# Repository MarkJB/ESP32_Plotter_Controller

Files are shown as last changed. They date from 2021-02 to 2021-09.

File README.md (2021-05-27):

# ESP32 Plotter Controller PCB
 
Released under an MIT licence, no warranty implied or given, use at own risk etc etc.

This is a two axis stepper controller based on the ESP32 and TMC2130 stepper drivers. It is intended to be used with drawing machines and plotters.

See https://github.com/MarkJB/TMC429_Daughterboard_for_ESP32_Plotter_Controller for the TMC429 (Hardware stepper driver contoller) daughter board for this board (plugs into the two stepper motor driver sockets and provides an extra axis and hardware acceleration control.

Firmware https://github.com/MarkJB/Grbl_Esp32 (This is a Fork of Grbl_Esp32, if its out of date, you probably only need the config file from this fork). Tested with standard and corexy kinematics and a solenoid/relay for the spindle.

First board revision A (aka 'Diamiond Chimp')

[Schematic]( https://github.com/MarkJB/ESP32_Plotter_Controller/blob/main/ESP32_Plotter_Controller_Schematic_RevA.pdf )

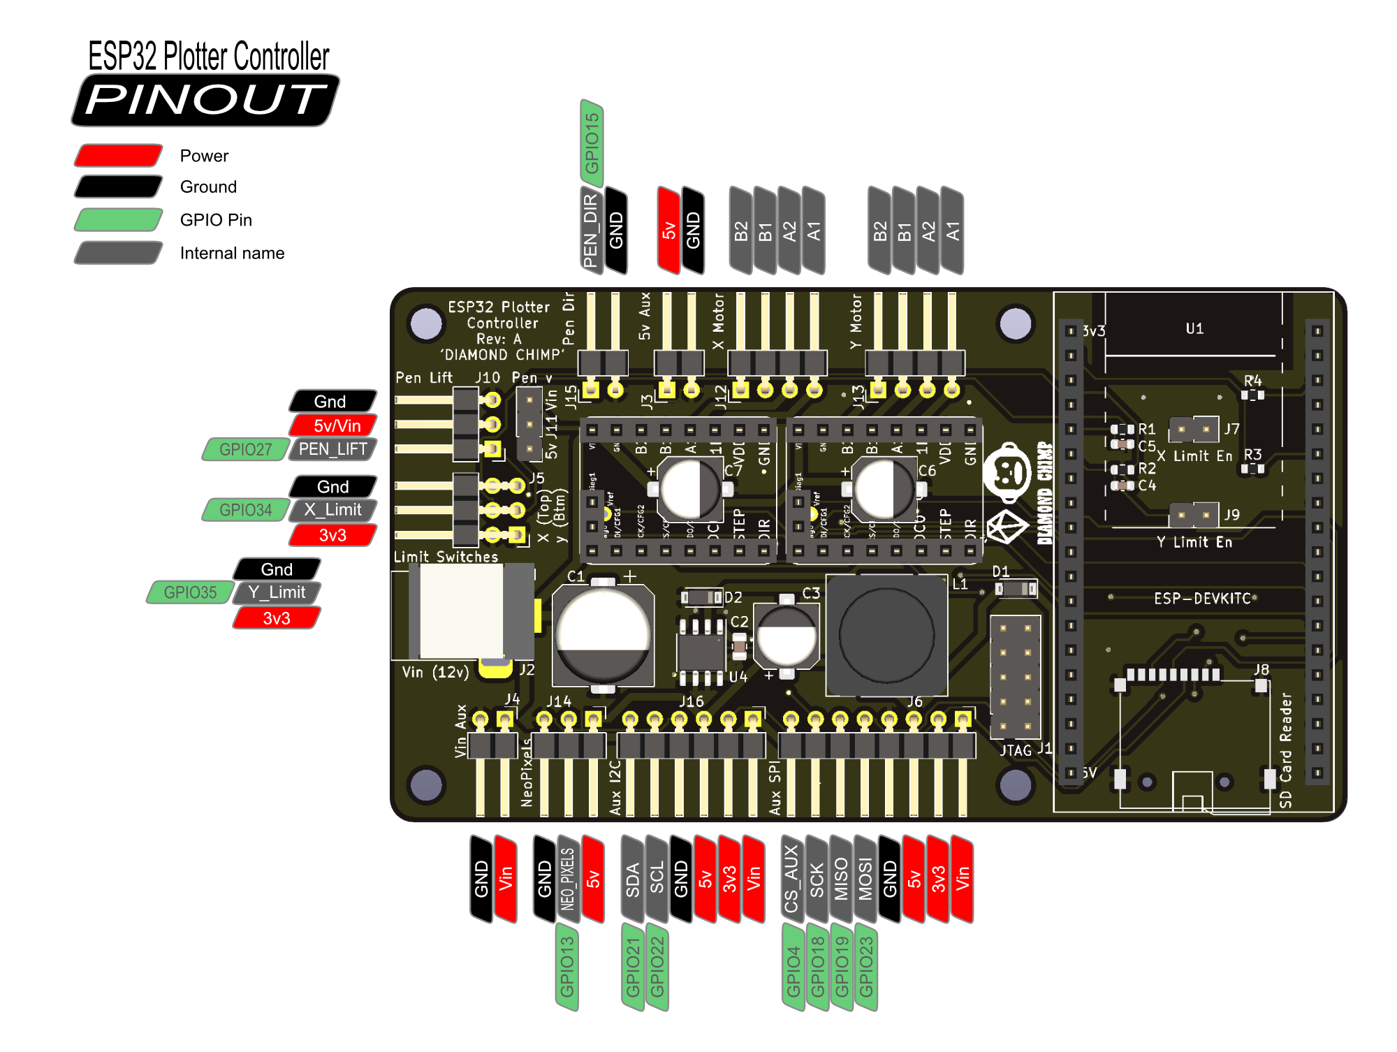
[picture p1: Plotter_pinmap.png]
Pinmap


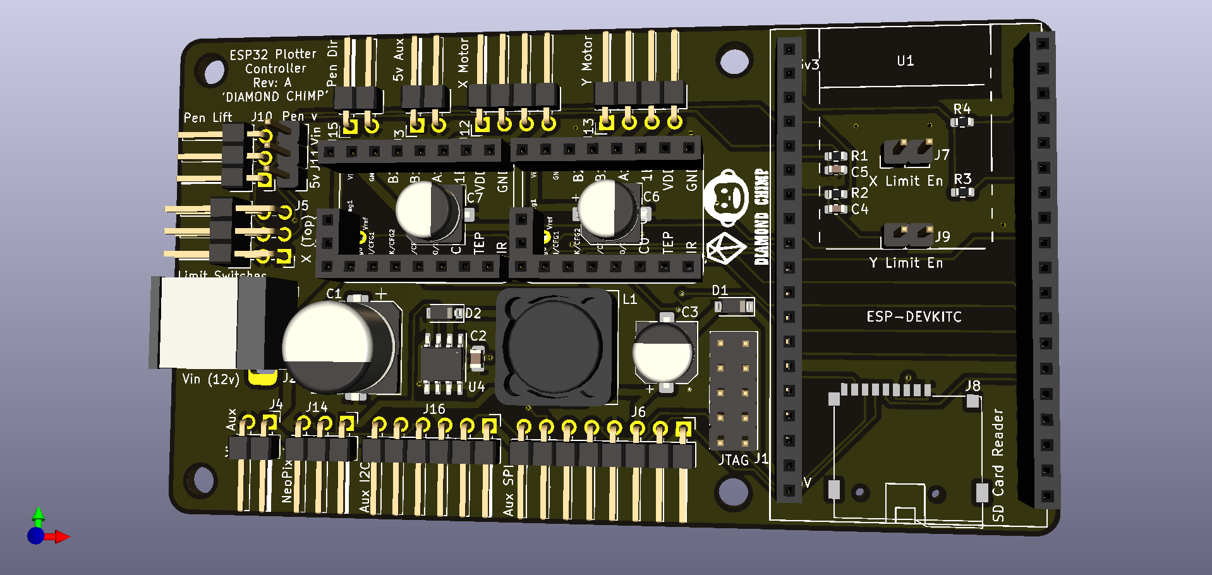
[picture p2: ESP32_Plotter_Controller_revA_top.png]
Render of top of board


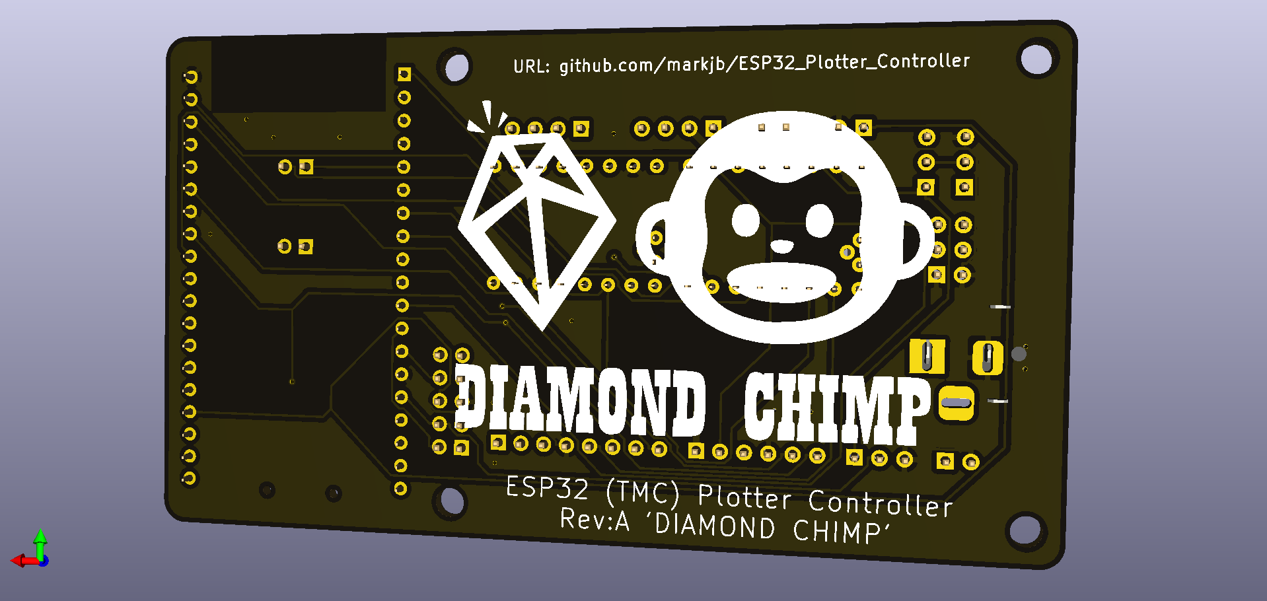
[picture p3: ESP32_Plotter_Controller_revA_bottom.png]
Render of bottom of board


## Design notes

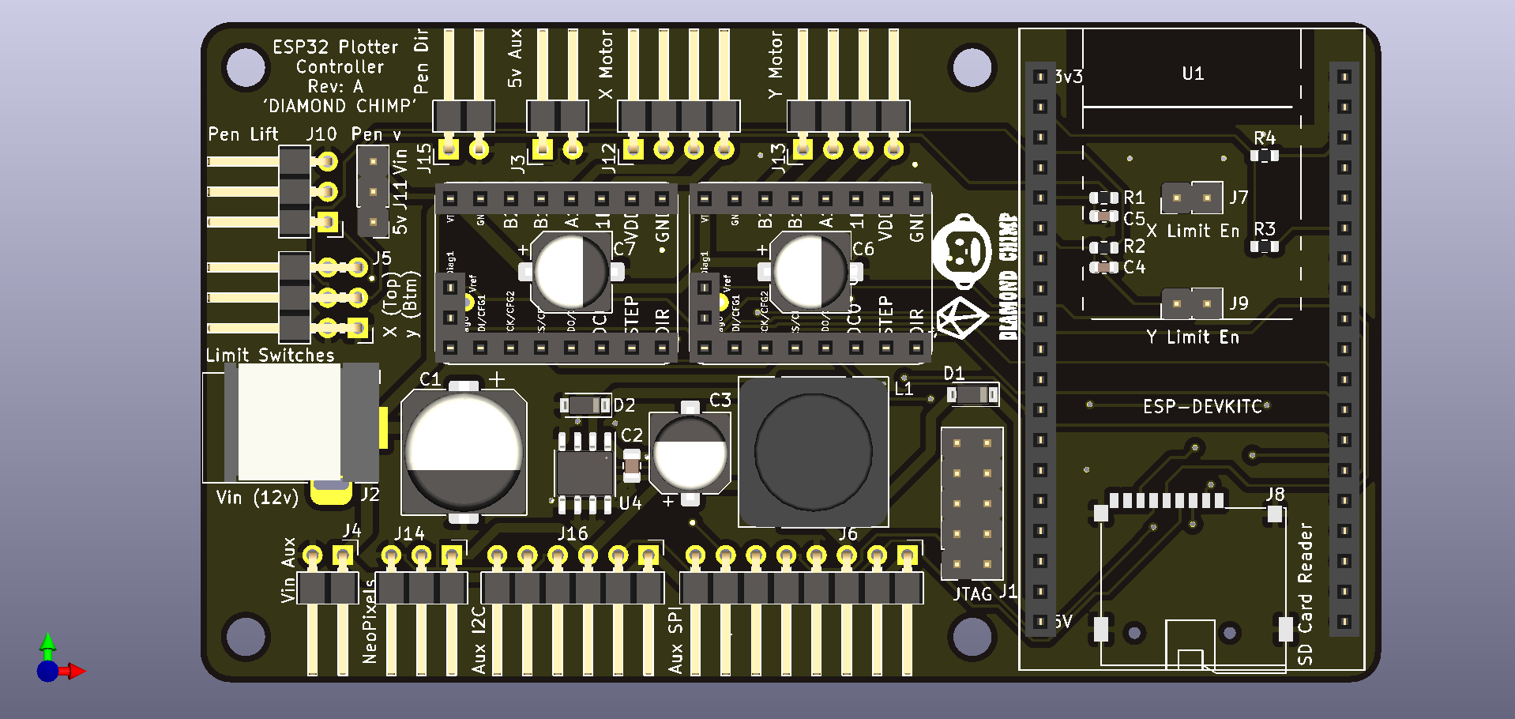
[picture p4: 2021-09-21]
ESP32_Plotter_Controller_revA_top_projection.png

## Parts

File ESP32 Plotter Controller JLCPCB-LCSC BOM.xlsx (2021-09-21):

 | ESP32 Plotter Controller parts cross check
 | PCB Part # | Value | Package | Board Note | Check Footprint | JLC part | JLC price | Package | LCSC part | LCSC price | Package | Qty (per board)
 | J1 | n/a | 5x2 vertical female 2.54mm | JTAG | TBD | No |  |  | C492399 | 0.1488 |  | 1
 | J2 | DC-005-20A | DC Barel jack | Power in | TBD | Yes | 0.179 | 14.2*9.0mm | C130239 | 0.1023 |  | 1
 | J3 | n/a | 2x1 right angle male 2.54mm | 5v aux | n/a | Yes | 0.0049 |  | C492410 | 0.012 |  | 1
 | J4 | n/a | 2x1 right angle male 2.54mm | 12v aux | n/a | Yes | 0.0049 |  | C492410 | 0.012 |  | 1
 | J5 | n/a | 3x2 right angle male 2.54mm | Limit Switches | n/a | No |  |  | C358705 | 0.0342 |  | 1
 | J6 | n/a | 8x1 right angle male 2.54mm | SPI port | n/a | No |  |  | C376126 | 0.0481 |  | 1
 | J7 | n/a | 2x1 vertical male 2.54mm | X Limit en | n/a | Yes | 0.0049 |  | C492401 | 0.0049 |  | 1
 | J8 | n/a | Micro SD card socket | SD card female | TBD | No |  |  | C91145 | 0.178 |  | 1
 | J9 | n/a | 2x1 vertical male 2.54mm | Y Limit en | n/a | Yes | 0.0049 |  | C492401 | 0.0049 |  | 1
 | J10 | n/a | 3x1 right angle male 2.54mm | Pen Lift | n/a | No |  |  | C492411 | 0.0199 |  | 1
 | J11 | n/a | 3x1 vertical male 2.54mm | Pen Lift voltage select | n/a | No |  |  | C306223 | 0.345 |  | 1
 | J12 | n/a | 4x1 right angle male 2.54mm | X Motor | n/a | No |  |  | C91552 | 0.0189 |  | 1
 | J13 | n/a | 4x1 right angle male 2.54mm | Y Motor | n/a | No |  |  | C91552 | 0.0189 |  | 1
 | J14 | n/a | 3x1 right angle male 2.54mm | Neo Pixels | n/a | No |  |  | C492411 | 0.0199 |  | 1
 | J15 | n/a | 2x1 right angle male 2.54mm | Pen Direction | n/a | Yes | 0.0049 |  | C492410 | 0.012 |  | 1
 | U1 | n/a | 19x1 vertical female 2.54mm | ESP32 DevkitC | TBD | No |  |  | C319202 | 0.1119 |  | 1
 | U1 | n/a | 19x1 vertical female 2.54mm | ESP32 DevkitC | TBD | No |  |  | C319202 | 0.1119 |  | 1
 | U2 | n/a | 8x1 vertical female 2.54mm | TMC2130 Stepper X | TBC | No |  |  | C429957 | 0.1119 |  | 1
 | U2 | n/a | 8x1 vertical female 2.54mm | TMC2130 Stepper X | TBC | No |  |  | C429957 | 0.0622 |  | 1
 | U2 | n/a | 2x1 vertical female 2.54mm | TMC2130 Stepper X | TBC | No |  |  | C541849 | 0.0723 |  | 1
 | U3 | n/a | 8x1 vertical female 2.54mm | TMC2130 Stepper Y | TBC | No |  |  | C429957 | 0.0622 |  | 1
 | U3 | n/a | 8x1 vertical female 2.54mm | TMC2130 Stepper Y | TBC | No |  |  | C429957 | 0.0622 |  | 1
 | U3 | n/a | 2x1 vertical female 2.54mm | TMC2130 Stepper Y | TBC | No |  |  | C541849 | 0.0723 |  | 1
 | U4 | XL1509 | SO-8_3.9x4.9mm_P1.27mm | DCDC converter | TBC |  |  |  | C61063 | 0.2268 |  | 1
 | D1 | B5819W | SOD-123 | Reverse current protection | TBC | Yes | 0.0344 | SOD-123 | C8598 | 0.0404 |  | 1
 | D2 | B5819W | SOD-123 | DCDC converter | TBC | Yes | 0.0344 | SOD-123 | C8598 | 0.0404 |  | 1
 | C1 | 470uF 25v SMT Elec | CP_ELEC_10x10 | DCDC converter | TBC | No |  |  | C280412 | 0.1255 |  | 1
 | C2 | 1uF 25v | 0805 | DCDC converter | TBC | Yes | 0.0526 |  | C28323 | 0.0163 |  | 1
 | C3 | 180uF 25v SMT Elec | CP_ELEC_6.3x7.7 | DCDC converter | TBC | Yes | 0.166 |  | C413657 | 0.3033 |  | 1
 | C4 | 100nF | 0603 | Y Limit debounce | TBC | No |  |  | C42998 | 0.0032 |  | 1
 | C5 | 100nF | 0603 | X Limit debounce | TBC | No |  |  | C42998 | 0.0032 |  | 1
 | C6 | 47uF | CP_ELEC_6.3x5.7 | Y Stepper resivoir | TBC |  |  |  | C176688 | 0.1016 |  | 1
 | C7 | 47uF | CP_ELEC_6.3x5.7 | X Stepper resivoir | TBC |  |  |  | C176688 | 0.1016 |  | 1
 | R1 | 100R | 0603 | X Limit debounce | TBC | Yes | 0.0013 |  | C25201 | 0.0013 |  | 1
 | R2 | 100R | 0603 | Y Limit debounce | TBC | Yes | 0.0013 |  | C25201 | 0.0013 |  | 1
 | R3 | 10K | 0603 | I2C Pull up (SDA) | TBC | No |  |  | C98220 | 0.0015 |  | 1
 | R4 | 10K | 0603 | I2C Pull up (SCL) | TBC | No |  |  | C98220 | 0.0015 |  | 1
 | L1 | 68uH 1.5A | SMD, 12.3x12.3x6mm | DCDC converter | TBC |  |  |  | C439406 | 0.232 |  | 1
 | PCB | Guestimate |  |  |  |  |  |  |  | 5
 | Assembly | Guestimate |  |  |  |  |  |  |  | 5
 |  |  |  |  |  |  |  |  |  | 12.8466
 | Component Order BOM (lcsc.com)
Ordered? | LCSC Part No: | Qty | PCB Part No: | Package | Value | Cost | Line Cost
n/a | C492399 | 1 | J1 | 5x2 vertical female 2.54mm |  | 0.1488 | 0.1488
Y | C130239 | 1 | J2 | DC Barrel jack |  | 0.1023 | 0.1023
no | C492410 | 2 | J3, J4, J15 | 2x1 right angle male 2.54mm |  | 0.012 | 0.024
Y | C358705 | 1 | J5 | 3x2 right angle male 2.54mm |  | 0.0342 | 0.0342
Y | C376126 | 1 | J6 | 8x1 right angle male 2.54mm |  | 0.0342 | 0.0342
Y | C492401 | 2 | J7, J9 | 2x1 vertical male 2.54mm |  | 0.0049 | 0.0098
Y | C492411 | 2 | J10, J14 | 3x1 right angle male 2.54mm |  | 0.0199 | 0.0398
Y | C306223 | 1 | J11 | 3x1 vertical male 2.54mm |  | 0.345 | 0.345
no | C91552 | 2 | J12, J13 | 4x1 right angle male 2.54mm |  | 0.0189 | 0.0378
Y | C91145 | 1 | J8 | Micro SD card socket |  | 0.178 | 0.178
Y | C319202 | 2 | U1 | 19x1 vertical female 2.54mm |  | 0.1119 | 0.2238
Y | C429957 | 4 | U2, U3 A | 8x1 vertical female 2.54mm |  | 0.1119 | 0.4476
Y | C541849 | 2 | U2, U3 B | 2x1 vertical female 2.54mm |  | 0.0723 | 0.1446
no | C61063 | 1 | U4 | SO-8_3.9x4.9mm_P1.27mm | XL1509 | 0.2268 | 0.2268
Y | C8598 | 2 | D1, D2 | SOD-123 | B5819W | 0.0404 | 0.0808
Y | C280412 | 1 | C1 | CP_ELEC_10x10 | 470uF 25v SMT Elec | 0.1255 | 0.1255
Y | C28323 | 1 | C2 | 0805 | 1uF 25v ceramic | 0.0163 | 0.0163
Y | C413657 | 1 | C3 | CP_ELEC_6.3x7.7 | 180uF 25v SMT Elec | 0.3033 | 0.3033
Y | C42998 | 2 | C4, C5 | 0603 | 100nF ceramic | 0.0032 | 0.0064
no | C176688 | 2 | C6, C7 | CP_ELEC_6.3x5.7 | 47uF 25v SMT Elec | 0.1016 | 0.2032
Y | C25201 | 2 | R1, R2 | 0603 | 100R | 0.0013 | 0.0026
Y | C98220 | 2 | R3, R4 | 0603 | 10k | 0.0015 | 0.003
Y | C439406 | 1 | L1 | L_12.3x12.3x6 SMT | 68uH 1.5A | 0.232 | 0.232
 |  |  |  |  |  |  | Total
 |  |  |  |  |  |  | 2.9698
 | Move capacitor nearer the dcdc chip, keep inductor feedback as short as possible, don't route under the inductor, connect en pin to via and leave floating

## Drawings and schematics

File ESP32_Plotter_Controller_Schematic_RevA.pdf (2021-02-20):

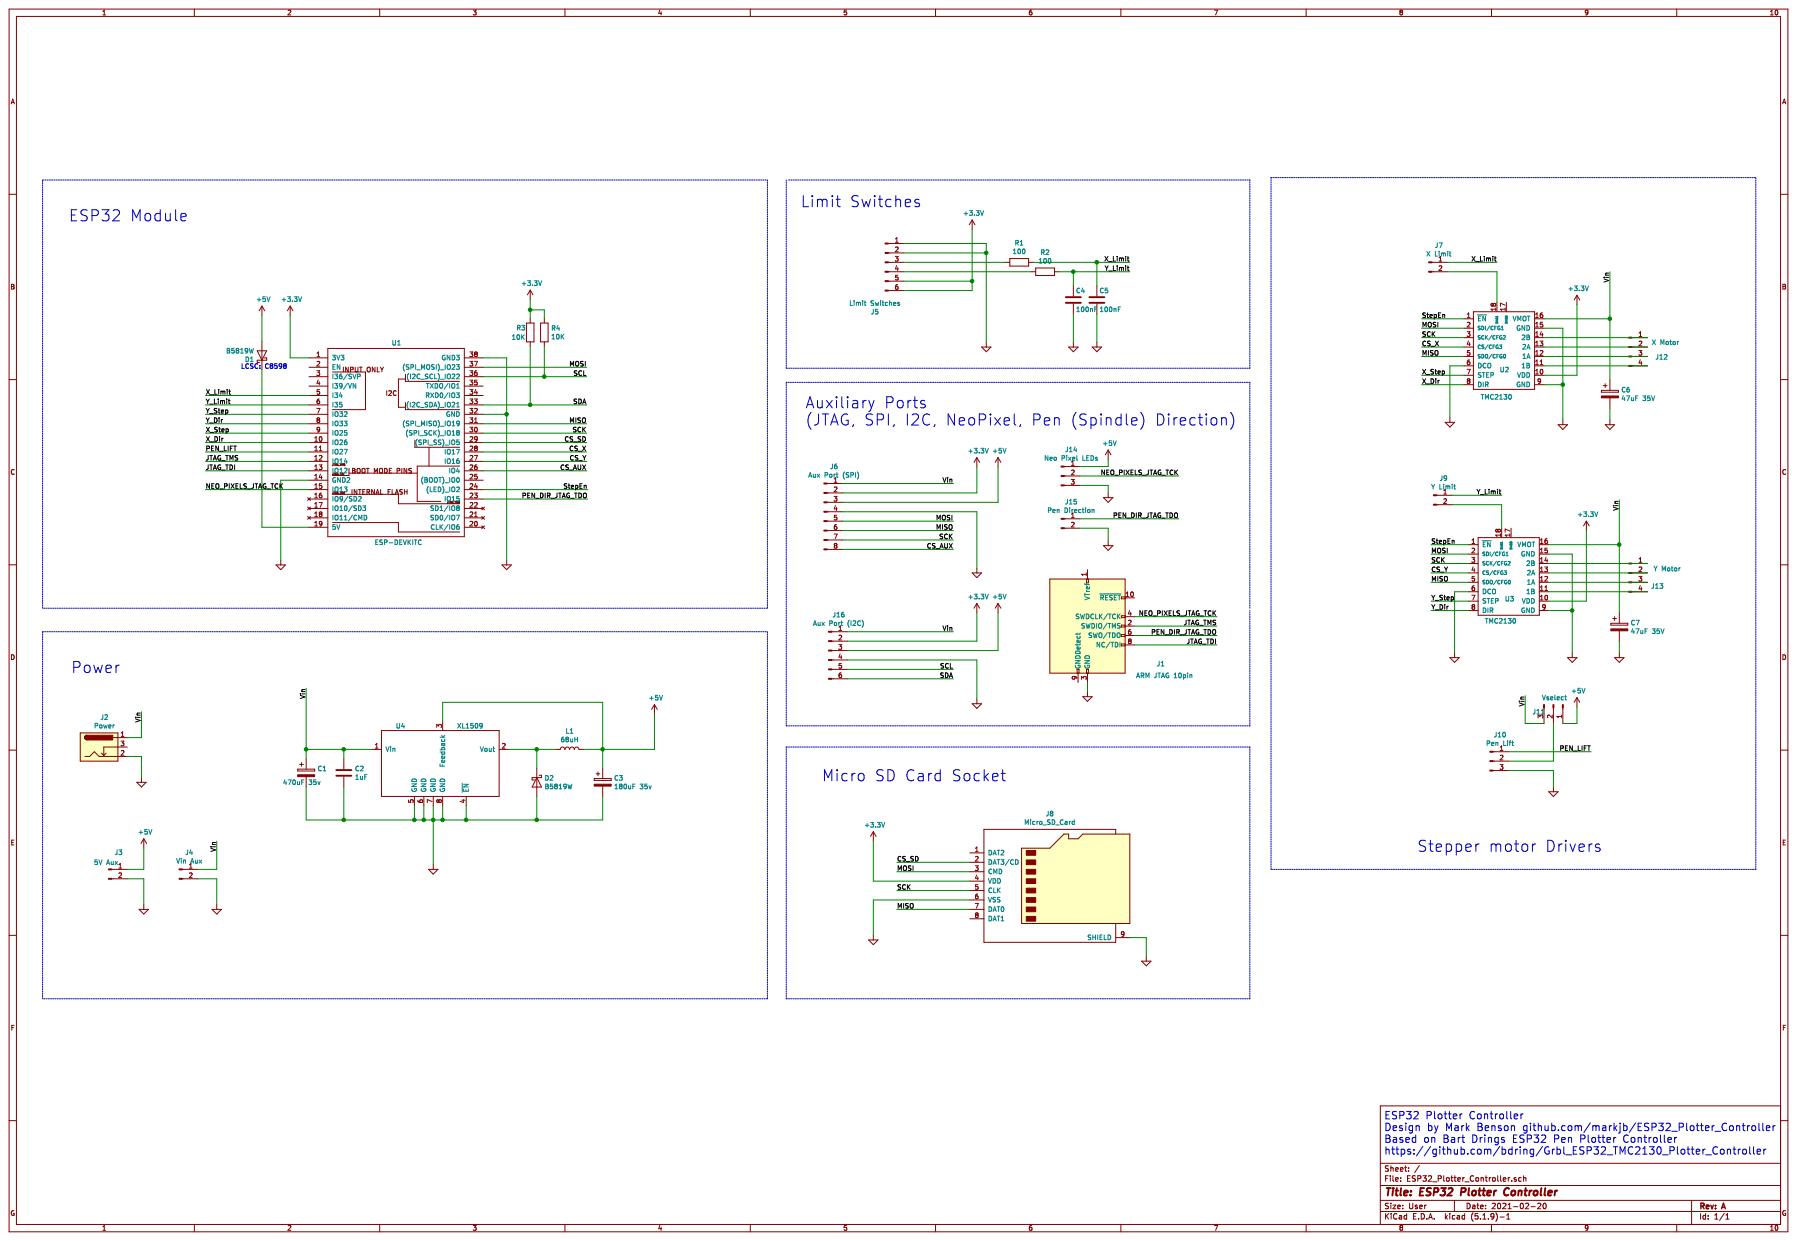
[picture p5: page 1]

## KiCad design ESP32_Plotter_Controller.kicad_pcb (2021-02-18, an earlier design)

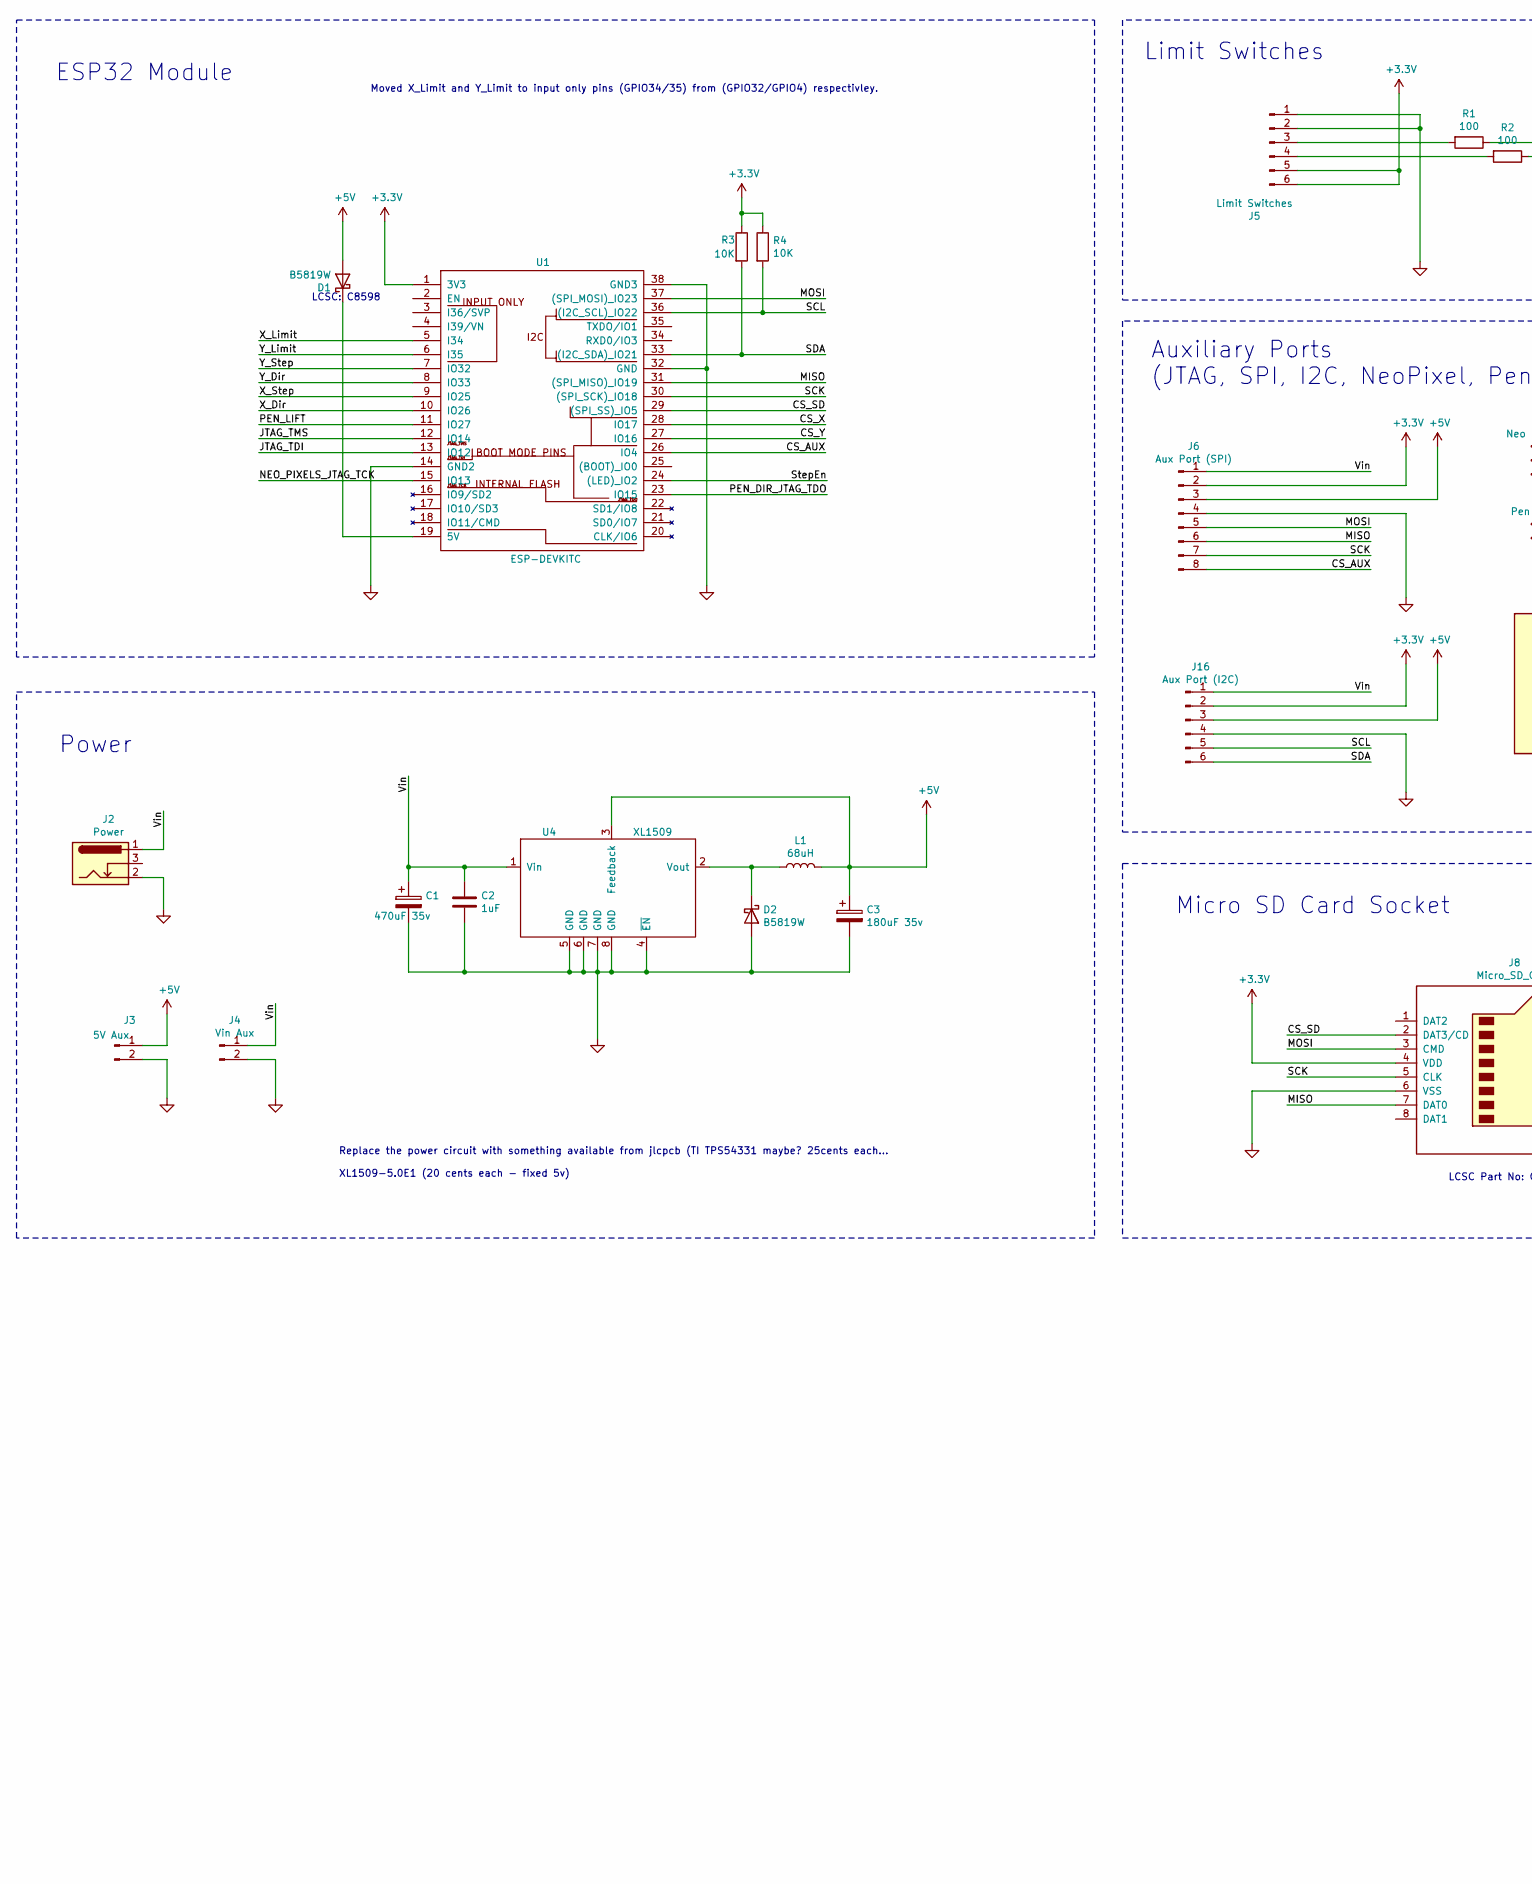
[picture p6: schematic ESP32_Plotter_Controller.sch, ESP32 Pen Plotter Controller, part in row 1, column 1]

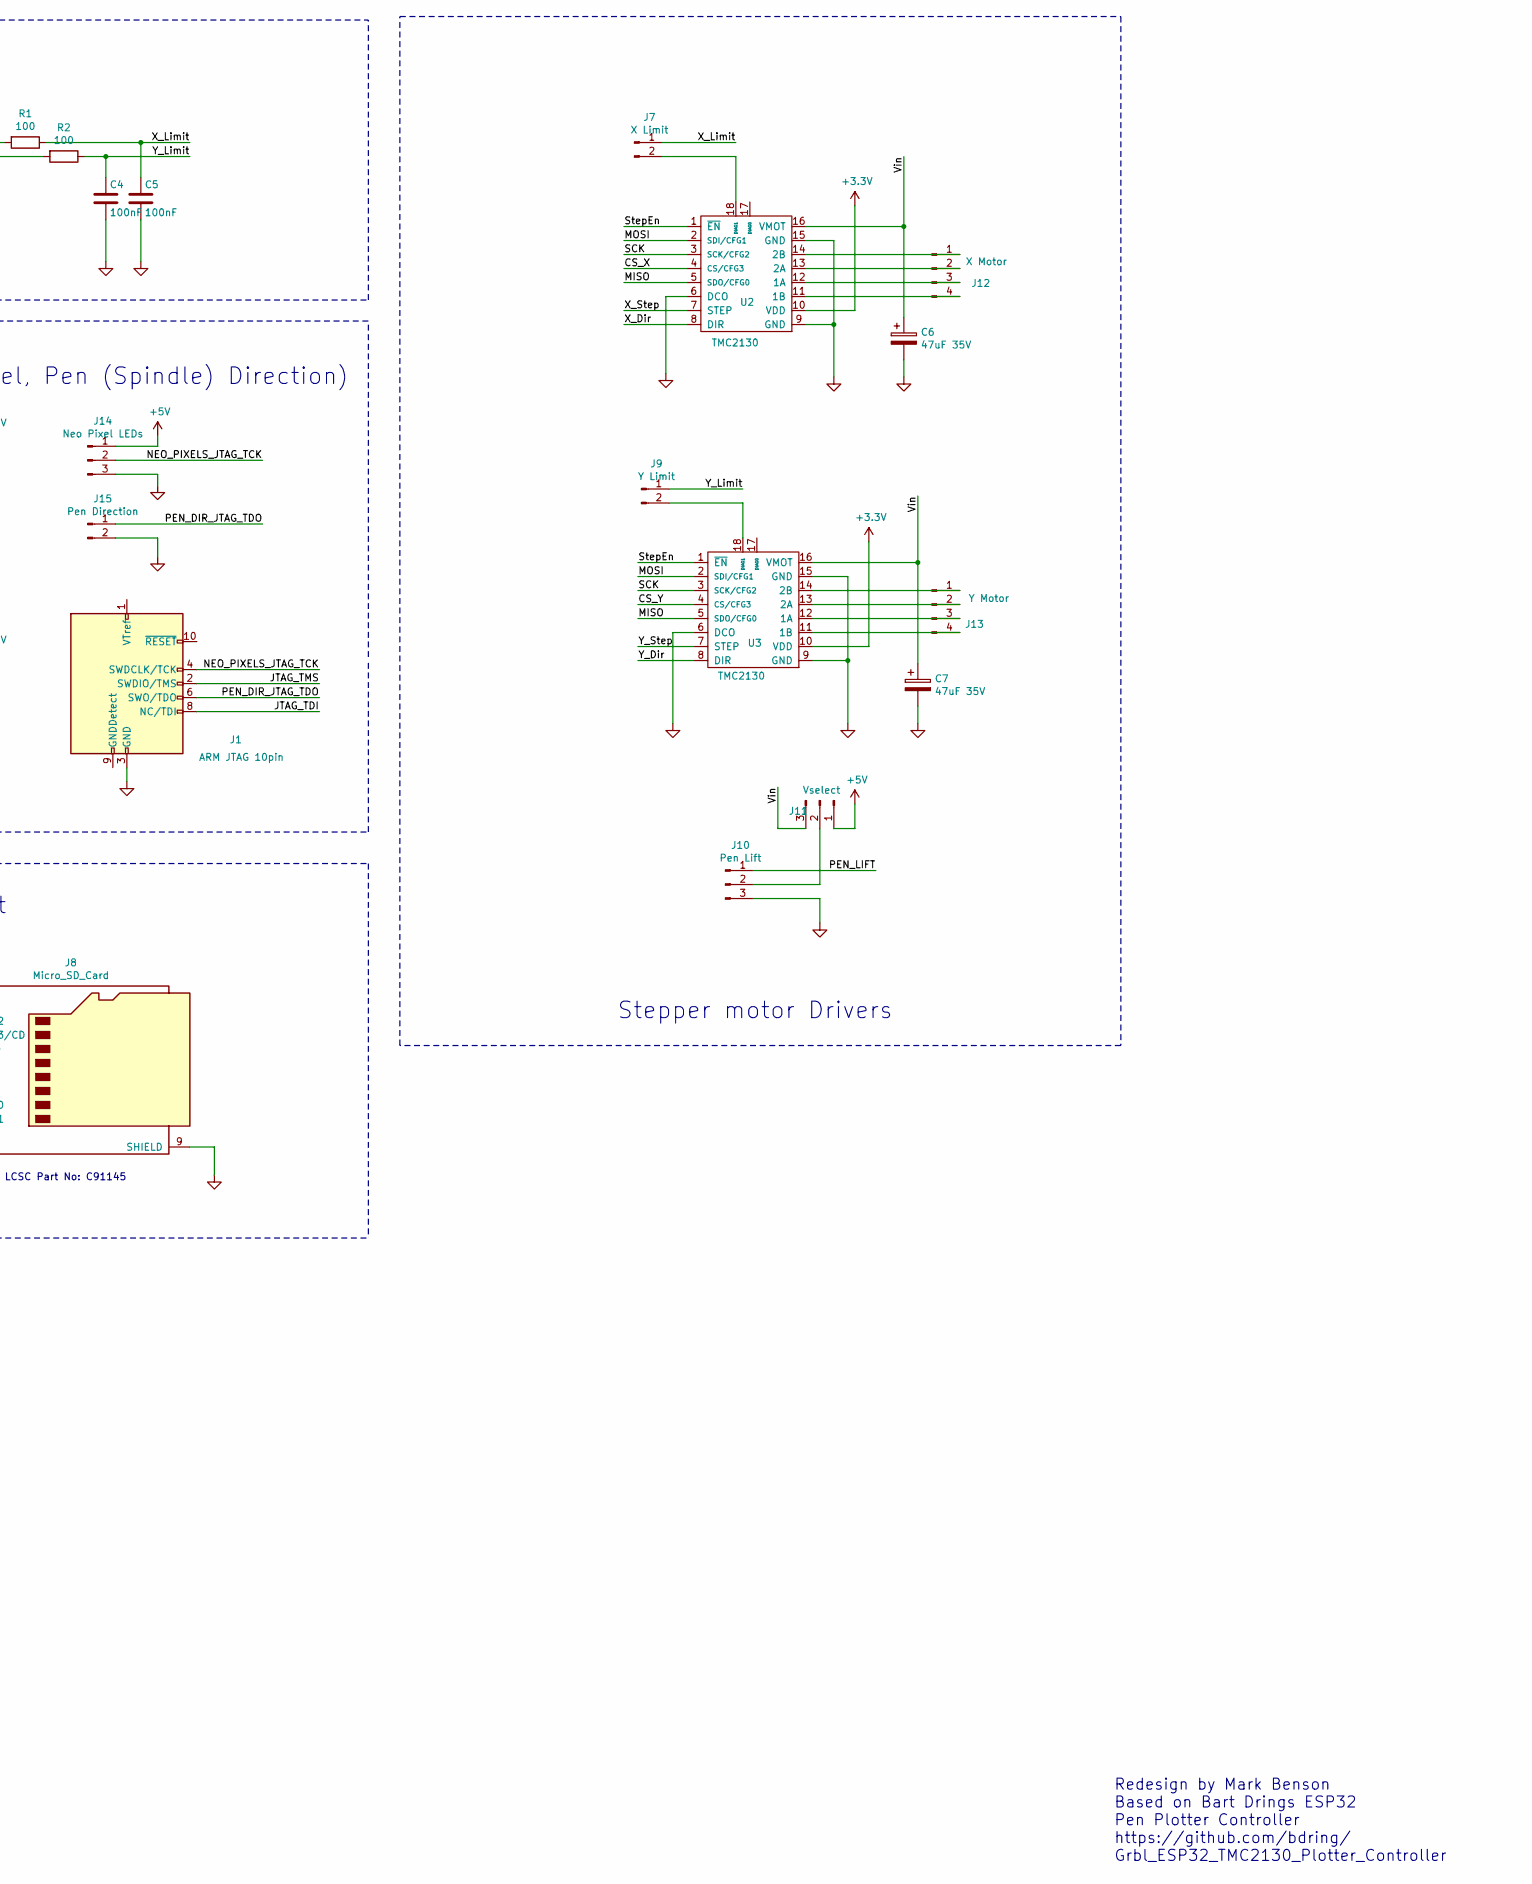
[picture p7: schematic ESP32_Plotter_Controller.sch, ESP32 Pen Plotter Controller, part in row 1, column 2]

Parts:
C1: 470uF 35v; CP_Elec_10x10
C2: 1uF; C_0805_2012Metric
C3: 180uF 35v; CP_Elec_6.3x7.7
C4, C5: 100nF; C_0603_1608Metric
C6, C7: 47uF 35V; CP_Elec_6.3x5.7
D1, D2: B5819W; D_SOD-123
J1: ARM JTAG 10pin; PinSocket_2x05_P2.54mm_Vertical
J2: Power; BarrelJack_Horizontal
J3: 5V Aux; PinHeader_1x02_P2.54mm_Horizontal
J4: Vin Aux; PinHeader_1x02_P2.54mm_Horizontal
J5: Limit Switches; PinHeader_2x03_P2.54mm_Horizontal
J6: Aux Port (SPI); PinHeader_1x08_P2.54mm_Horizontal
J7: X Limit; PinHeader_1x02_P2.54mm_Vertical
J8: Micro_SD_Card; HK-TF01A
J9: Y Limit; PinHeader_1x02_P2.54mm_Vertical
J10: Pen Lift; PinHeader_1x03_P2.54mm_Horizontal
J11: Vselect; PinHeader_1x03_P2.54mm_Vertical
J12: X Motor; PinHeader_1x04_P2.54mm_Horizontal
J13: Y Motor; PinHeader_1x04_P2.54mm_Horizontal
J14: Neo Pixel LEDs; PinHeader_1x03_P2.54mm_Horizontal
J15: Pen Direction; PinHeader_1x02_P2.54mm_Horizontal
J16: Aux Port (I2C); PinHeader_1x06_P2.54mm_Horizontal
L1: 68uH; L_12x12mm_H6mm
R1, R2: 100; R_0603_1608Metric
R3, R4: 10K; R_0603_1608Metric
U1: ESP-DEVKITC; DEVKITC
U2, U3: TMC2130; StepstickTMCv2
U4: XL1509; SO-8_3.9x4.9mm_P1.27mm

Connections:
+3V3: J5.5, J5.6, J6.2, J8.4 (VDD), J16.2, R3.1, R4.1, U1.1 (3V3), U2.10 (VDD), U3.10 (VDD)
+5V: C3.1, D1.2 (A), J3.1, J6.3, J11.1, J14.1, J16.3, L1.2, U4.3 (Feedback)
/CS_AUX: J6.8, U1.26 (IO4)
/CS_SD: J8.2 (DAT3/CD), U1.29 ((SPI_SS)_IO5)
/CS_X: U1.28 (IO17), U2.4 (CS/CFG3)
/CS_Y: U1.27 (IO16), U3.4 (CS/CFG3)
/JTAG_TDI: J1.8 (NC/TDI), U1.13 (IO12)
/JTAG_TMS: J1.2 (SWDIO/TMS), U1.12 (IO14)
/MISO: J6.6, J8.7 (DAT0), U1.31 ((SPI_MISO)_IO19), U2.5 (SDO/CFG0), U3.5 (SDO/CFG0)
/MOSI: J6.5, J8.3 (CMD), U1.37 ((SPI_MOSI)_IO23), U2.2 (SDI/CFG1), U3.2 (SDI/CFG1)
/NEO_PIXELS_JTAG_TCK: J1.4 (SWDCLK/TCK), J14.2, U1.15 (IO13)
/PEN_DIR_JTAG_TDO: J1.6 (SWO/TDO), J15.1, U1.23 (IO15)
/PEN_LIFT: J10.1, U1.11 (IO27)
/SCK: J6.7, J8.5 (CLK), U1.30 ((SPI_SCK)_IO18), U2.3 (SCK/CFG2), U3.3 (SCK/CFG2)
/SCL: J16.5, R4.2, U1.36 ((I2C_SCL)_IO22)
/SDA: J16.6, R3.2, U1.33 ((I2C_SDA)_IO21)
/StepEn: U1.24 ((LED)_IO2), U2.1 (~EN), U3.1 (~EN)
/Vin: C1.1, C2.1, C6.1, C7.1, J2.1, J4.1, J6.1, J11.3, J16.1, U2.16 (VMOT), U3.16 (VMOT), U4.1 (Vin)
/X_Dir: U1.10 (IO26), U2.8 (DIR)
/X_Limit: C5.1, J7.1, R1.1, U1.5 (I34)
/X_Step: U1.9 (IO25), U2.7 (STEP)
/Y_Dir: U1.8 (IO33), U3.8 (DIR)
/Y_Limit: C4.1, J9.1, R2.1, U1.6 (I35)
/Y_Step: U1.7 (IO32), U3.7 (STEP)
GND: C1.2, C2.2, C3.2, C4.2, C5.2, C6.2, C7.2, D2.2 (A), J1.3 (GND), J1.5 (GND), J2.2, J3.2, J4.2, J5.1, J5.2, J6.4, J8.6 (VSS), J8.9 (SHIELD), J10.3, J14.3, J15.2, J16.4, U1.14 (GND2), U1.32 (GND), U1.38 (GND3), U2.6 (DCO), U2.9 (GND), U2.15 (GND), U3.6 (DCO), U3.9 (GND), U3.15 (GND), U4.4 (~EN), U4.5 (GND), U4.6 (GND), U4.7 (GND), U4.8 (GND)
unnamed: D1.1 (K), U1.19 (5V)
unnamed: D2.1 (K), L1.1, U4.2 (Vout)
unnamed: J5.3, R1.2
unnamed: J5.4, R2.2
unnamed: J7.2, U2.18 (DIAG1)
unnamed: J9.2, U3.18 (DIAG1)
unnamed: J10.2, J11.2
unnamed: J12.1, U2.14 (2B)
unnamed: J12.2, U2.13 (2A)
unnamed: J12.3, U2.12 (1A)
unnamed: J12.4, U2.11 (1B)
unnamed: J13.1, U3.14 (2B)
unnamed: J13.2, U3.13 (2A)
unnamed: J13.3, U3.12 (1A)
unnamed: J13.4, U3.11 (1B)

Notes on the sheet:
Micro SD Card Socket
Limit Switches
Stepper motor Drivers
ESP32 Module
Power
Replace the power circuit with something available from jlcpcb (TI TPS54331 maybe? 25cents each... XL1509-5.0E1 (20 cents each - fixed 5v)
LCSC: C8598
Redesign by Mark Benson Based on Bart Drings ESP32 Pen Plotter Controller https://github.com/bdring/ Grbl_ESP32_TMC2130_Plotter_Controller
Auxiliary Ports (JTAG, SPI, I2C, NeoPixel, Pen (Spindle) Direction)
Moved X_Limit and Y_Limit to input only pins (GPIO34/35) from (GPIO32/GPIO4) respectivley.
LCSC Part No: C91145

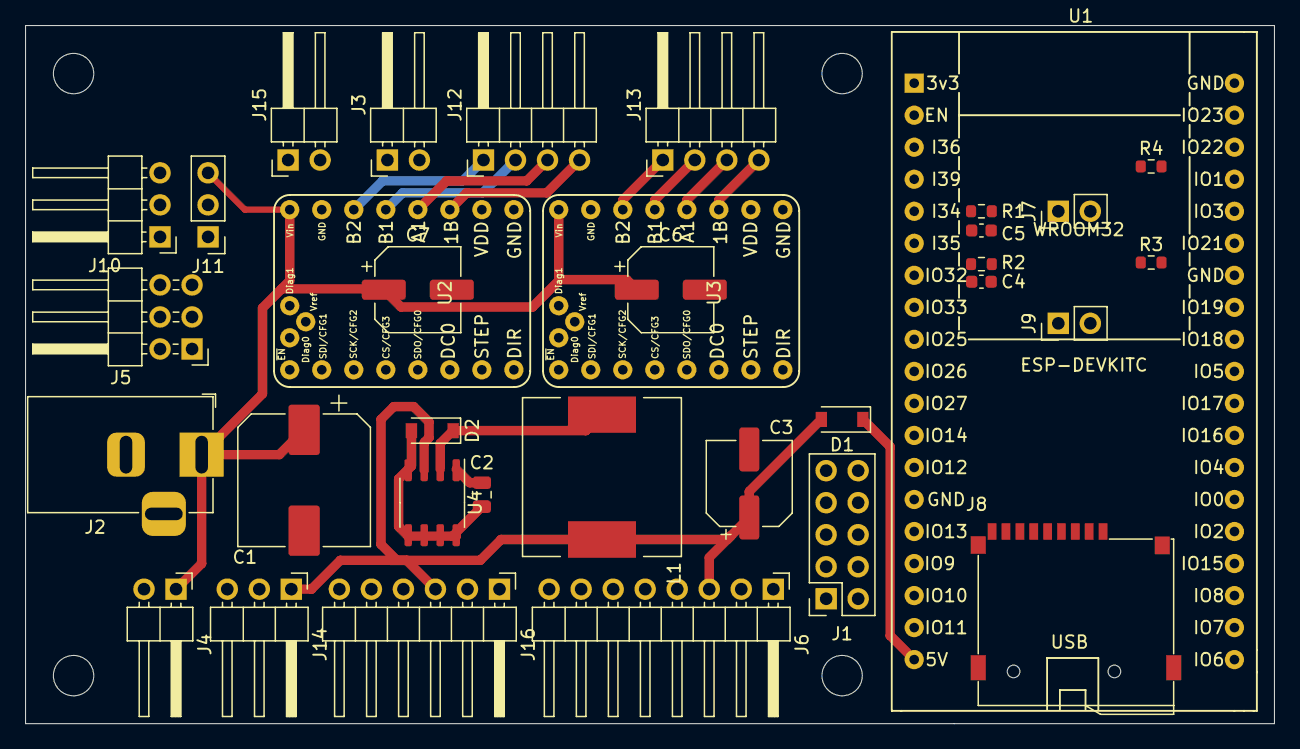
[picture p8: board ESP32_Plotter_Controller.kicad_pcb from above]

Board: 2 copper layers, 99.1 x 55.4 mm, 38 parts (0 on the bottom side), 40 nets.

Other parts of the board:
H1, H2, H3, H4: MountingHole_3.2mm_M3

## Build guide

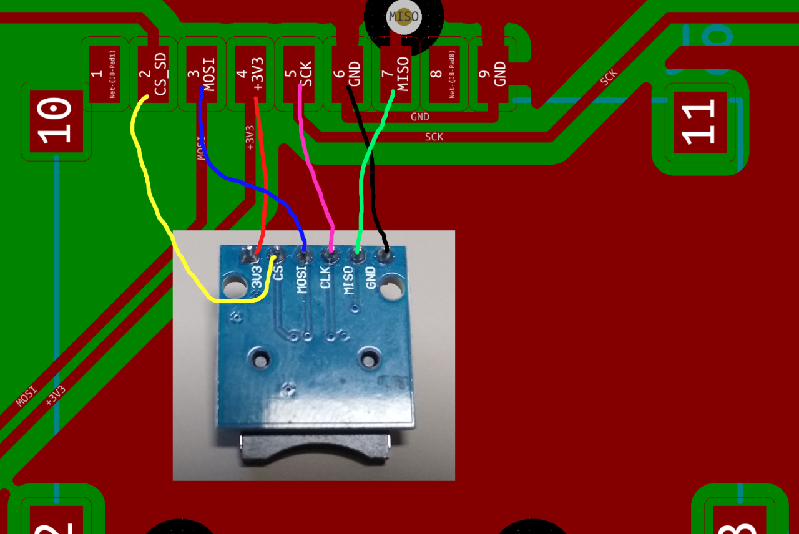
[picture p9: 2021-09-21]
temp_sdcard_wiring.png

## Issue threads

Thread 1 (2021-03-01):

DCDC converter needs reworking

MarkJB, 2021-03-01:
Feedback track should not go under the inductor and tracks should be as short as possible.

MarkJB, 2021-03-04:
Fixed in commit abf19ead8a0773d469e5b664175c62ed65a1bd63

Closed 2021-03-04.

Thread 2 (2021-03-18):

Future PCB code name - cause thats important right?

MarkJB, 2021-03-18:
So we have confidence that Rev A is perfect and there are no mistakes! But just incase, here are some code names for future revisions :)

Based on: Gemstone: Animal

Rev A: Diamond Chimp
Rev B: Emerald Dingo
Rev C: Fledspar Emu
Rev D: Garnet Frog
Rev E: Hellenite Gopher

MarkJB, 2021-05-27:
Closing for now as I think we have enough code names :)

Closed 2021-05-27.

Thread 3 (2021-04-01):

SD card footprint pin ordering incorrect

MarkJB, 2021-04-01:
Pin ordering for the SD card footprint is reversed.

MarkJB, 2021-04-05:
Fixed by commit 43fb1d9

Closed 2021-04-05.

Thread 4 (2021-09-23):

StallGuard not working

MarkJB, 2021-09-23:
Current working theory is the TMC2130 Diag1 pin is open drain and the input pins on the ESP32 do not have internal pull up resistors so they are just floating.

Need to add external pull up resistors.

MarkJB, 2021-09-25:
Issue confirmed. Tested StallGuard with and without 10k pull-up resistors and it only works with... :(

MarkJB, 2022-01-10:
Jumping the endstop connectors isn't going to be as easy on RevB (as its using JST PH2.0 connectors) and would also require changing the 100R resistors (basically a lot of faff).

Added R9 & R10 (10k) pull-up resistors which are permenantly connected to Diag1 of the TMC2130s. This way we can still use mechanical limit switches that have their own pull-up circuitry (e.g. makerbot end-stops) by not jumpering J7 & J9 (pull-ups not in-circuit).

Changes made on RevB with fe3bdf5

Closed 2022-01-10.

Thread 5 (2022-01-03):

Connector silkscreeen missing on RevB

MarkJB, 2022-01-03:
The labels for the connectors are missing - probably on a layer that wasn't seen as silkscreen.

Note: This applies to the Rev B PCB.

MarkJB, 2022-01-10:
Not really an issue. It was because the option to plot 'values' was not checked when plotting the gerber files (I was following the jlcpcb gerber production guide and didn't think about the effect it would have)

A silly mistake to make - need to pay more attention when running files thru the gerber viewer before pulling the pin on PCB manuacture!

Closed 2022-01-10.

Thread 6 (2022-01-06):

Can't program ESP32 on RevB

MarkJB, 2022-01-06:
Serial coms is present but esptool timesout with `Failed to connect to ESP32: Timed out waiting for packet header`.

SW2 = Boot = IO0
SW1 = Reset = EN

EN and IO0 appear to be held low... (which is what the buttons are supposed to do)

MarkJB, 2022-01-09:
I missed a 10k pull-up resistor on EN. Also added one to IO0 just in case, but testing suggests that in unnecessary.

Closed 2022-01-09.

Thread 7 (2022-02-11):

RevB USB comms speed limited

MarkJB, 2022-02-11:
Should have routed the traces as a differential pair.

MarkJB, 2022-02-11:
Rerouted tracks for USB d+/-.
New board works at 921600 baud. May work at higher baud rates but not tested.

Closed 2022-02-11.

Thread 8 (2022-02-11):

SD card insertion resets USB comms

MarkJB, 2022-02-11:
When plugging in an SD card the serial comms disconnect. The ESP32 appears to continue running and the SD card can be read.

Have added more decoupling but that has worked.

I'm a bit stumpped about this one.

MarkJB, 2022-02-13:
From vscode serial monitor:

`--- Miniterm on COM9  115200,8,N,1 ---
--- Quit: Ctrl+C | Menu: Ctrl+T | Help: Ctrl+T followed by Ctrl+H ---

ok
ok
Exception in thread rx:
Traceback (most recent call last):
  File "C:\Users\mark\.platformio\python3\lib\threading.py", line 954, in _bootstrap_inner
    self.run()
  File "C:\Users\mark\.platformio\python3\lib\threading.py", line 892, in run
    self._target(*self._args, **self._kwargs)
  File "C:\Users\mark\.platformio\penv\lib\site-packages\serial\tools\miniterm.py", line 499, in reader
    data = self.serial.read(self.serial.in_waiting or 1)
  File "C:\Users\mark\.platformio\penv\lib\site-packages\serial\serialwin32.py", line 295, in read
    raise SerialException("GetOverlappedResult failed ({!r})".format(ctypes.WinError()))
serial.serialutil.SerialException: GetOverlappedResult failed (PermissionError(13, 'Access is denied.', None, 5))`

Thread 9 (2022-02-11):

RevB C15 is in way of screw head

MarkJB, 2022-02-11:
Capacitor C15 will be in the way of mounting screw.

Need to see if it can be moved out of the way.

Closed 2022-02-13.

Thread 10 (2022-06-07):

Solenoid connector pin out wrong on pin map

MarkJB, 2022-06-07:
The gnd and en pins are swapped on the pin map

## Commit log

2021-02-18 Clean up
    [ESP32_Plotter_Controller_r1-brd.dxf]
2021-02-20 Clean up folder
    [ESP32_Plotter_Controller.sch, sdcard.FCStd]
2021-02-20 Clean up, add repo name
    [ESP32 Plotter Controller JLCPCB-LCSC BOM.xlsx, ESP32_Plotter_Controller.sch, ESP32_Plotter_Controller_revA.kicad_pcb]
2021-02-20 Removed unused models and foot prints
    [OBJ_NEW_PCB.obj]
2021-03-04 Fix DCDC track layout
    [ESP32 Plotter Controller JLCPCB-LCSC BOM.xlsx, ESP32_Plotter_Controller_r1.kicad_pcb, ESP32_Plotter_Controller_revA.kicad_pcb]
2021-03-08 Increased thickness of 5v track to J3
    J3 (5v Aux) was a 0.25mm track. Increased to 0.4mm.
    [ESP32_Plotter_Controller_revA.kicad_pcb]
2021-04-05 Fix sdcard footprint
    Fix mirrored pinout on SD Card footprint.
    Also grounded shield in schematic and disconnected the sd insert sense pin from gnd.
    [ESP32_Plotter_Controller.sch, ESP32_Plotter_Controller_revA.kicad_pcb]
2021-04-15 Pinmap & new grber files for sd card fix
    [ESP32_Plotter_Controller_revA-B_Cu.gbr, ESP32_Plotter_Controller_revA-B_Mask.gbr, ESP32_Plotter_Controller_revA-B_Paste.gbr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]
2021-09-21 Misc changes
    Not sure what I changed here, but the current production boards were made from this set of files.
    [ESP32 Plotter Controller JLCPCB-LCSC BOM.xlsx, ESP32_Plotter_Controller.sch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]
